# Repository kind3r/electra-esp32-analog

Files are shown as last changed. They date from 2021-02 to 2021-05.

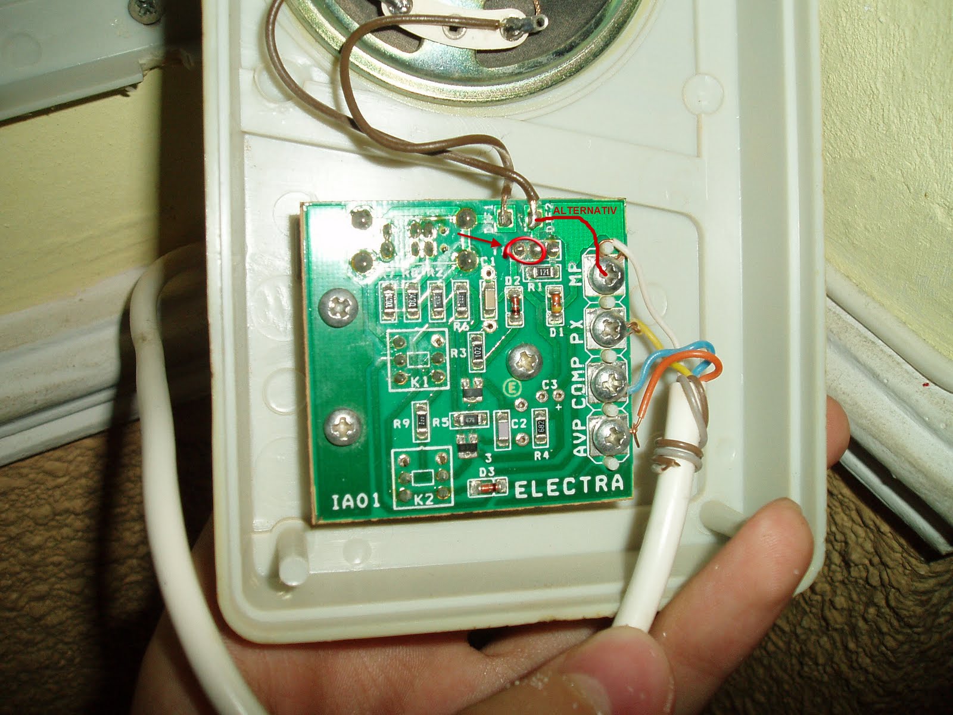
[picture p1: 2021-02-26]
docs/IA02-undressed.JPG

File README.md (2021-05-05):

# electra-esp32-analog

Turning an analogic Electra IA003/IA01/IA02 into a smart Home Assistant [lock device](https://www.home-assistant.io/integrations/lock/) using an ESP32-WROOM-32D module and a few extra components.

> **WARNING**: This project is a work in progress. Use at own risk.

Feeling generous and want to support my work, here is [my PayPal link](https://paypal.me/kind3r).

## Intro

After some research and experimentation it was **not possible to power the ESP32 module from the intercom power line** as the power is not always available and the ESP32 WiFi and boot power drain spikes confuse the Electra Call Distributor. So the next logical step was to use a battery to power the device. 

Regular **rechargeable Li-Ion** batteries are commonly available ini different shapes and sizes. The problem is that they charge up to about 4.2V so they require some voltage drop to be able to power the ESP32. Since the device only wakes up when the intercom is riniging and voltage drop circuit consumes power all the time, this makes using such batteries inefficient (and I am a big fan of optimisation). There are of course more efficient LDO's like TI's [TPS62841DGRR](https://ro.mouser.com/ProductDetail/595-TPS62841DGRR) but those are hard to find currently.

At first I opted for a rechargeable **LiFePO4 18650** battery to optimise power usage since it's nominal voltage is 3.2V and it's max charge is 3.6V, thus it does not require power regulation which saves quite some energy. Combined with the fact that the device is mostly in deep sleep mode, this should give a **very long battery life** (few years - still need to make exact measuremets). Unfortunatelly LiFePO4 batteries and chargers (I had to build my own) do not seem to be that common making which raises the cost of (also time to build) the device. 

Now I am testing 2 **alkaline AAA** batteries and it seems to work fine and they also fit in the intercom case, event better than the 18650 but due to their discharge curve only about 30% of their capacity will be used (which still would provide up to a year of usage). But then you are throwinig away 2/3 of the battery (unless you move it to a remote control or some other AAA powered device). Not ideal. 

Another option would be using **lithium AAA** batteries which are available locally (not as much as alkaline AAA, but still). While a bit more expensive than the regular alkaline AAA, their discharge curve is optimal for powering the ESP32, providinig a similar life to the rechargeable LiFePO4. 

## Features

- Easy configuration via Soft AP and browser UI
  - Automatically enter config mode in case of errors
  - Manually enter config mode using dedicated button
- [Home Assistant](https://www.home-assistant.io/) integration via MQTT
  - Ringing status
  - Unlock
  - Battery life reporting
  - Configure automations
- Ultra low power usage
  - Deep sleep when not ringing
  - Deep sleep after 5 min if in configuration mode 
- LED status
  - Slow blink: Configuration mode
  - Fast blink: Ringing
- Optically isolated from intercom's lines, no risk of damaging the ESP32 module
- Fits inside the intercom's enclosure

## How To

### Build your device

Schematic, PCB and BOM are available [here](https://oshwlab.com/Gibonii/electra-ia003-ia01-esp). 

> **WARNING**: Schematic and PCB not yet final, I might still make adjustments. Rev.4 is currently under testing and working fine. 

> TODO: how to order PCBs and assembly

> TODO: explain extra components required:
> - JST-SH-6 + VoltLink or USB2TTL
> - JST-SH-3 for intercom interface
> - JST-XH-2 and LiFePO4 battery + holder

### Upload software

> TODO: 
> - Connector for uploading
> - How to build and make configuration adjustments (battery reporting interval, configuration mode sleep time)
> - PlatformIO + upload SPIFFS (for web config) & config file (optional)

### Configuration

> TODO: 
> - HA preparations
> - First time configuration
> - Testing

## Resources of inspiration

- [https://micro-flight.blogspot.com/2010/09/hack-interfon-electra.html](https://micro-flight.blogspot.com/2010/09/hack-interfon-electra.html)
- [https://forum.arduino.cc/index.php?topic=659051.0](https://forum.arduino.cc/index.php?topic=659051.0)

## TODO

Short term:
- Finish documentation
- Test power usage

Medium/long term:
- Make a changelog
- Provide other integrations besides Home Assistant

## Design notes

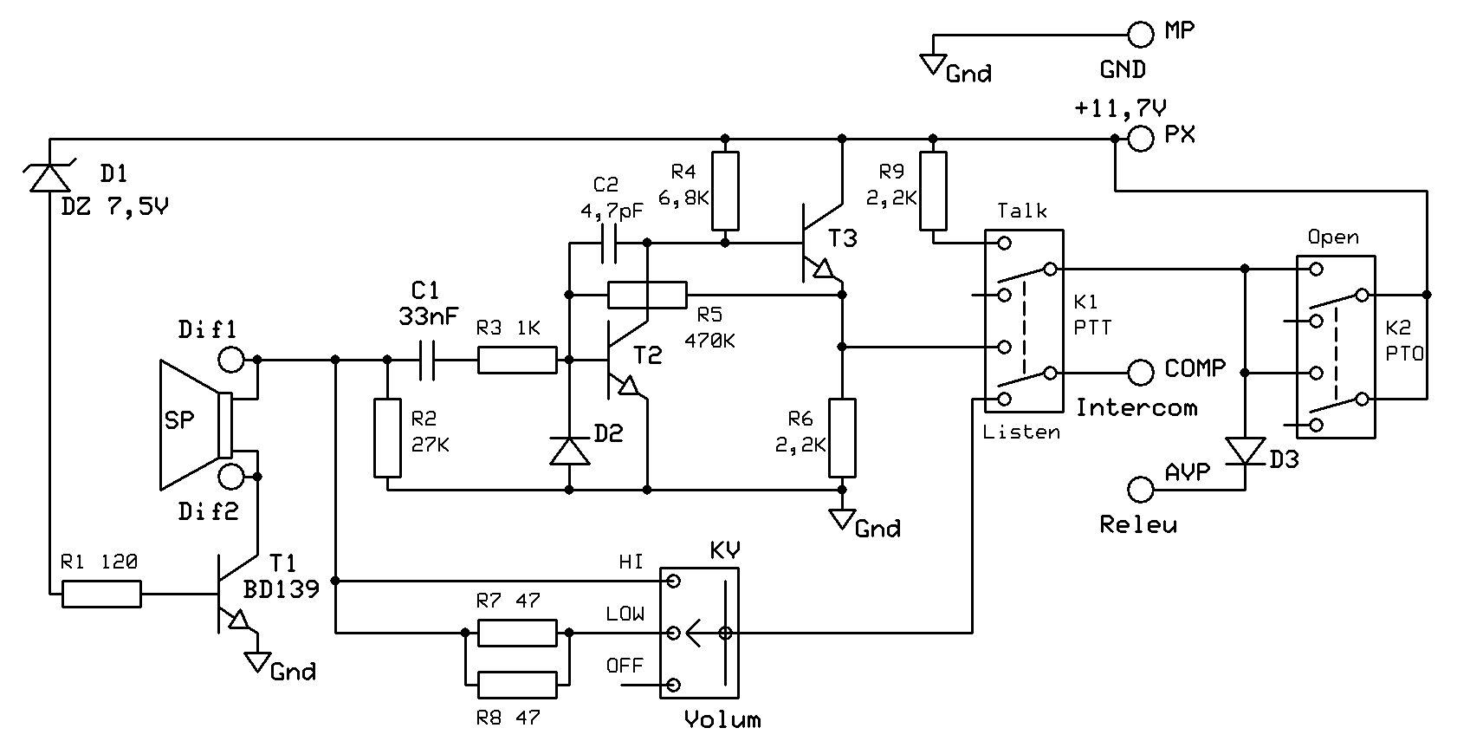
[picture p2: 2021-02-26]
docs/IA02-circuit.jpg

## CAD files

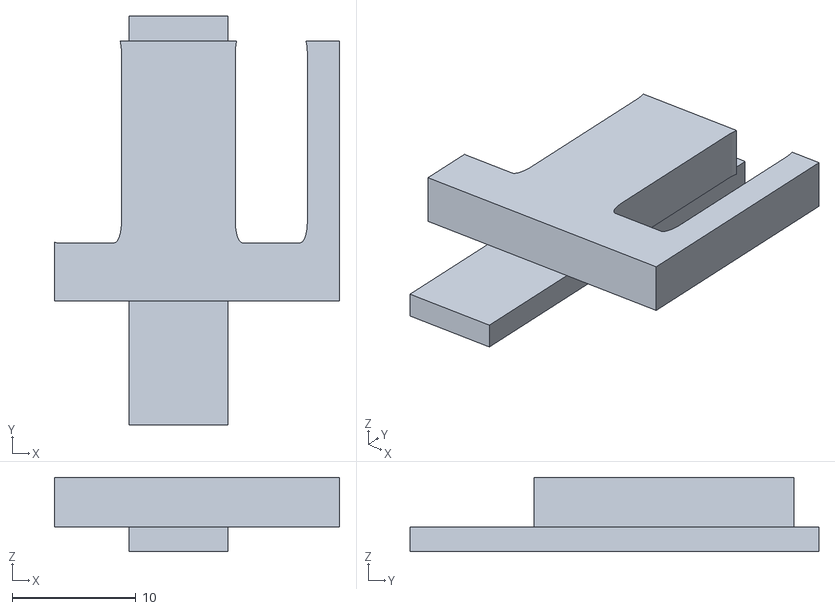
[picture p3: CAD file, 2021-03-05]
docs/other/Electra IA001 Buttons cover.stl
23.0 x 33.0 x 6.00

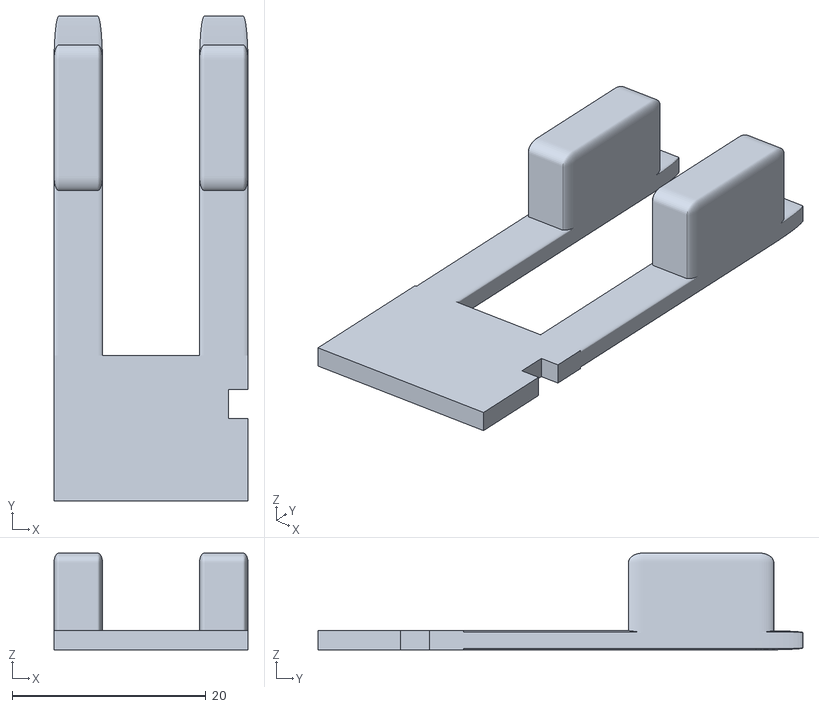
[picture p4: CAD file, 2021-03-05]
docs/other/Electra IA001 Buttons.stl
20.0 x 50.0 x 10.0

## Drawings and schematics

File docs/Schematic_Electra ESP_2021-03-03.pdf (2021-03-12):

## Intercom control

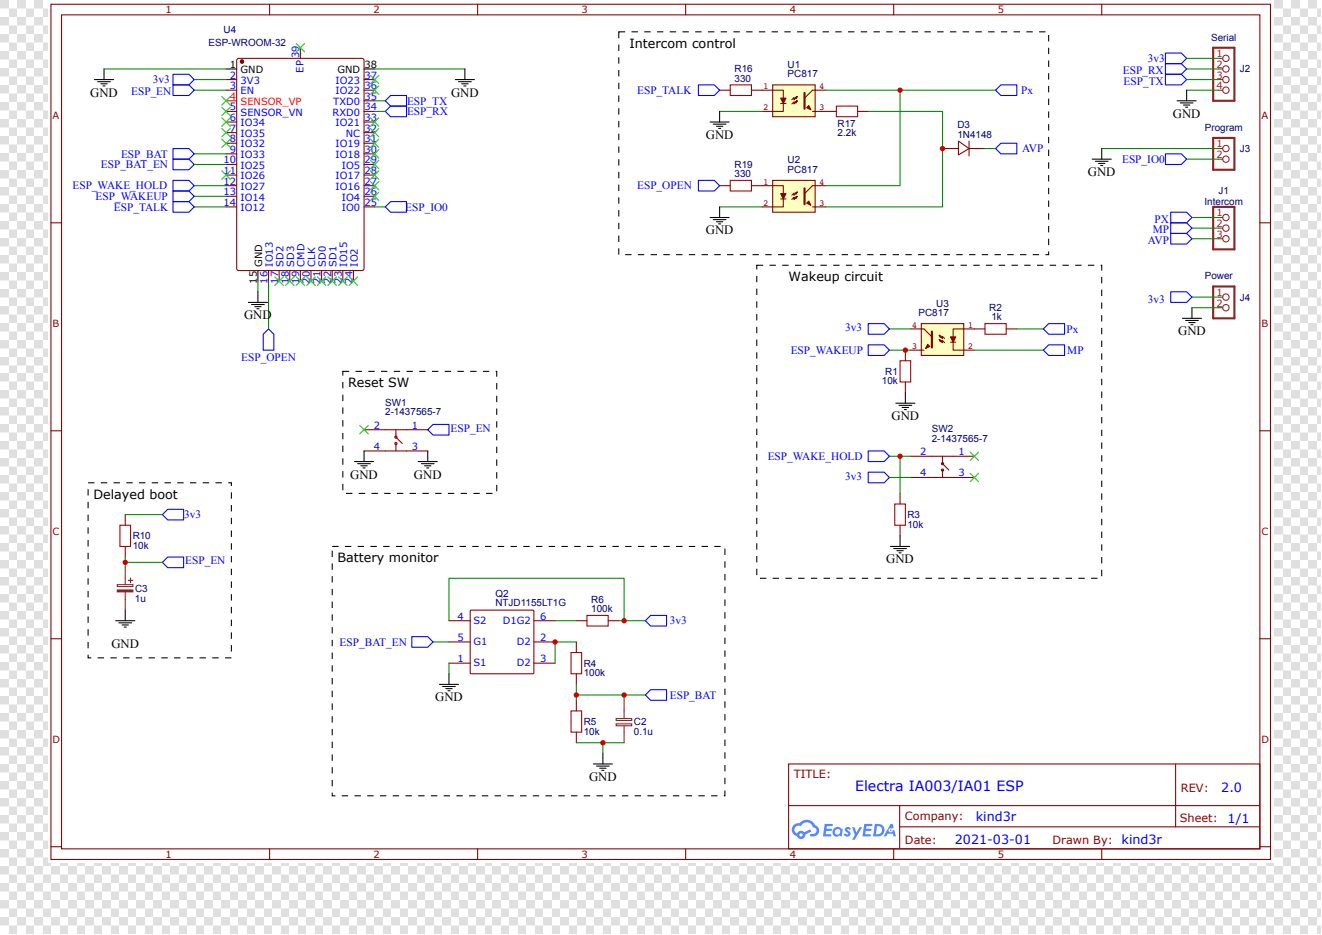
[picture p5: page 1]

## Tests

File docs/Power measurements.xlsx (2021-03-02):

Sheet: 240Mhz, 2654ms
Voltage-Current
Time | Voltage(V) | Current(A) | D+(V) | D-(V) | Date | Absolute (mA)
0.3016898148 | 4.98 | 0.017 | 3.07 | 0.18 | 44254 | 0
0.3017013889 | 4.98 | 0.017 | 3.06 | 0.19 | 44254 | 0
0.301712963 | 4.98 | 0.017 | 3.07 | 0.19 | 44254 | 0
0.301724537 | 4.98 | 0.019 | 3.08 | 0.19 | 44254 | 2
0.3017361111 | 4.96 | 0.06 | 3.05 | 0.19 | 44254 | 43
0.3017476852 | 4.95 | 0.084 | 3.07 | 0.19 | 44254 | 67
0.3017592593 | 4.95 | 0.084 | 3.08 | 0.19 | 44254 | 67
0.3017708333 | 4.96 | 0.062 | 3.06 | 0.19 | 44254 | 45
0.3017824074 | 4.96 | 0.058 | 3.07 | 0.18 | 44254 | 41
0.3017939815 | 4.95 | 0.099 | 3.07 | 0.17 | 44254 | 82
0.3018055556 | 4.96 | 0.075 | 3.07 | 0.2 | 44254 | 58
0.3018171296 | 4.96 | 0.066 | 3.06 | 0.2 | 44254 | 49
0.3018287037 | 4.96 | 0.074 | 3.07 | 0.19 | 44254 | 57
0.3018402778 | 4.96 | 0.065 | 3.07 | 0.2 | 44254 | 48
0.3018518519 | 4.96 | 0.067 | 3.07 | 0.18 | 44254 | 50
0.3018634259 | 4.97 | 0.017 | 3.06 | 0.18 | 44254 | 0
0.301875 | 4.98 | 0.018 | 3.07 | 0.18 | 44254 | 1
0.3018865741 | 4.98 | 0.017 | 3.06 | 0.18 | 44254 | 0
0.3018981481 | 4.97 | 0.017 | 3.07 | 0.2 | 44254 | 0
0.3019097222 | 4.98 | 0.017 | 3.06 | 0.19 | 44254 | 0
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

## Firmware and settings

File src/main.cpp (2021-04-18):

#include <esp_err.h>
#include <nvs_flash.h>
#include <esp_netif.h>
#include <esp_event.h>
#include "settings.h"
#include "ha.h"
#include "wifi.h"
#include "wifiap.h"
#include "util.h"
#include "intercom.h"
#include "sleep.h"
#include "battery.h"
#include "led.h"
#include "ota.h"
#include "spiffs.h"
#include "log.h"

extern "C"
{
  void app_main(void);
}

void app_main()
{
  ESP_ERROR_CHECK(nvs_flash_init());
  ESP_ERROR_CHECK(esp_netif_init());
  ESP_ERROR_CHECK(esp_event_loop_create_default());

  Spiffs::init();
  
  LOG::init();
  
  Led::init();

  Battery::init();

  Intercom::init();

  Sleep::init();

  if (Settings::init() != ESP_OK)
  {
    ESP_LOGE("main", "Error during Settings init");
    // enter config mode
    WiFiAP::init();
    Sleep::start(300); // sleep after 5 minutes
  }
  else
  {
    Ota::init();
    if (HA::init() != ESP_OK)
    {
      ESP_LOGE("main", "Error during HA init");
      Sleep::start();
    }
    else if (WiFi::init() != ESP_OK)
    {
      ESP_LOGE("main", "Error during WiFi init");
      // Sleep::start();
      esp_restart();
    }
  }
}

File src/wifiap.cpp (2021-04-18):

#include "wifiap.h"
#include "dnsserver.h"

static const char *TAG = "WiFiAP";

httpd_handle_t WiFiAP::server = nullptr;
httpd_uri_t WiFiAP::home = {
    .uri = "/",
    .method = HTTP_GET,
    .handler = handleHome,
    .user_ctx = NULL};
httpd_uri_t WiFiAP::configGet = {
    .uri = "/config",
    .method = HTTP_GET,
    .handler = handleConfigGet,
    .user_ctx = NULL};
httpd_uri_t WiFiAP::configSet = {
    .uri = "/config",
    .method = HTTP_POST,
    .handler = handleConfigSet,
    .user_ctx = NULL};
httpd_uri_t WiFiAP::logsGet = {
    .uri = "/logs",
    .method = HTTP_GET,
    .handler = handleLogsGet,
    .user_ctx = NULL};
httpd_uri_t WiFiAP::logGet = {
    .uri = "/log/*",
    .method = HTTP_GET,
    .handler = handleLogGet,
    .user_ctx = NULL};
uint8_t *WiFiAP::buffer = new uint8_t[ELECTRA_ESP_CONFIG_BUFFER_SIZE];
logFiles_t WiFiAP::logs;

void WiFiAP::init()
{
  mdns_start();
  wifi_init_softap();
  Led::blinkSlow();
}

void WiFiAP::startWebServer()
{
  if (server == nullptr)
  {
    httpd_config_t config = HTTPD_DEFAULT_CONFIG();
    config.max_open_sockets = 3;
    config.uri_match_fn = httpd_uri_match_wildcard;
    // config.stack_size = 8192;

    httpd_start(&server, &config);
    httpd_register_uri_handler(server, &home);
    httpd_register_uri_handler(server, &configGet);
    httpd_register_uri_handler(server, &configSet);
    httpd_register_uri_handler(server, &logsGet);
    httpd_register_uri_handler(server, &logGet);
  }
}

void WiFiAP::event_handler(void *arg, esp_event_base_t event_base, int32_t event_id, void *event_data)
{
  if (event_base == WIFI_EVENT && event_id == WIFI_EVENT_STA_START)
  {
    esp_wifi_connect();
  }
  else if (event_id == WIFI_EVENT_AP_STACONNECTED)
  {
    wifi_event_ap_staconnected_t *event = (wifi_event_ap_staconnected_t *)event_data;
    ESP_LOGI(TAG, "station " MACSTR " join, AID=%d", MAC2STR(event->mac), event->aid);
    startWebServer();
  }
  else if (event_id == WIFI_EVENT_AP_STADISCONNECTED)
  {
    wifi_event_ap_stadisconnected_t *event = (wifi_event_ap_stadisconnected_t *)event_data;
    ESP_LOGI(TAG, "station " MACSTR " leave, AID=%d", MAC2STR(event->mac), event->aid);
  }
}

void WiFiAP::wifi_init_softap()
{
  esp_netif_create_default_wifi_ap();

  wifi_init_config_t cfg = WIFI_INIT_CONFIG_DEFAULT();
  ESP_ERROR_CHECK(esp_wifi_init(&cfg));

  ESP_ERROR_CHECK(esp_event_handler_instance_register(WIFI_EVENT,
                                                      ESP_EVENT_ANY_ID,
                                                      &event_handler,
                                                      NULL,
                                                      NULL));

  wifi_config_t wifi_config = {};
  strcpy((char *)wifi_config.ap.ssid, ELECTRA_ESP_WIFI_CONFIG_SSID);
  wifi_config.ap.ssid_len = strlen(ELECTRA_ESP_WIFI_CONFIG_SSID);
  strcpy((char *)wifi_config.ap.password, ELECTRA_ESP_WIFI_CONFIG_PASS);
  wifi_config.ap.channel = ELECTRA_ESP_WIFI_CONFIG_CHANNEL;
  wifi_config.ap.max_connection = ELECTRA_ESP_WIFI_CONFIG_MAX_CONNECTIONS;
  wifi_config.ap.authmode = WIFI_AUTH_WPA2_PSK;

  ESP_ERROR_CHECK(esp_wifi_set_mode(WIFI_MODE_AP));
  ESP_ERROR_CHECK(esp_wifi_set_config(WIFI_IF_AP, &wifi_config));
  ESP_ERROR_CHECK(esp_wifi_start());

  ESP_LOGI(TAG, "wifi_init_softap finished. SSID:%s password:%s channel:%d",
           ELECTRA_ESP_WIFI_CONFIG_SSID, ELECTRA_ESP_WIFI_CONFIG_PASS, ELECTRA_ESP_WIFI_CONFIG_CHANNEL);

  // Setup DNS server to respond to name.local
  char hostname[strlen(ELECTRA_ESP_WIFI_HOSTNAME) + 7];
  memcpy(hostname, ELECTRA_ESP_WIFI_HOSTNAME, strlen(ELECTRA_ESP_WIFI_HOSTNAME));
  memcpy(hostname + strlen(ELECTRA_ESP_WIFI_HOSTNAME), ".local", 6);
  hostname[strlen(ELECTRA_ESP_WIFI_HOSTNAME) + 7] = '\0';
  init_dns_server(hostname);
}

esp_err_t WiFiAP::handleHome(httpd_req_t *req)
{
  FILE *fd = nullptr;
  fd = fopen("/spiffs/index.html.gz", "r");
  if (!fd)
  {
    ESP_LOGE(TAG, "Failed to read index.html.gz from SPIFFS");
    /* Respond with 500 Internal Server Error */
    httpd_resp_send_err(req, HTTPD_500_INTERNAL_SERVER_ERROR, "Failed to read existing file");
    return ESP_FAIL;
  }

  // set content type and encoding
  httpd_resp_set_type(req, "text/html");
  httpd_resp_set_hdr(req, "Content-Encoding", "gzip");

  /* Retrieve the pointer to scratch buffer for temporary storage */
  size_t chunksize;
  do
  {
    /* Read file in chunks into the scratch buffer */
    chunksize = fread(buffer, 1, ELECTRA_ESP_CONFIG_BUFFER_SIZE, fd);

    if (chunksize > 0)
    {
      /* Send the buffer contents as HTTP response chunk */
      if (httpd_resp_send_chunk(req, (char *)buffer, chunksize) != ESP_OK)
      {
        fclose(fd);
        ESP_LOGE(TAG, "File sending failed!");
        /* Abort sending file */
        httpd_resp_sendstr_chunk(req, NULL);
        /* Respond with 500 Internal Server Error */
        httpd_resp_send_err(req, HTTPD_500_INTERNAL_SERVER_ERROR, "Failed to send file");
        return ESP_FAIL;
      }
    }

    /* Keep looping till the whole file is sent */
  } while (chunksize != 0);

  /* Send empty chunk to signal HTTP response completion */
  httpd_resp_sendstr_chunk(req, NULL);

  fclose(fd);

  return ESP_OK;
}

esp_err_t WiFiAP::handleConfigGet(httpd_req_t *req)
{
  httpd_resp_set_type(req, HTTPD_TYPE_JSON);

  size_t len = Settings::getConfigFile(buffer);
  buffer[len] = '\0';

  httpd_resp_sendstr(req, (char *)buffer);

  return ESP_OK;
}

esp_err_t WiFiAP::handleConfigSet(httpd_req_t *req)
{
  int total_len = req->content_len;
  int cur_len = 0;
  int received = 0;
  if (total_len >= ELECTRA_ESP_CONFIG_BUFFER_SIZE)
  {
    /* Respond with 500 Internal Server Error */
    httpd_resp_send_err(req, HTTPD_500_INTERNAL_SERVER_ERROR, "content too long");
    return ESP_FAIL;
  }
  while (cur_len < total_len)
  {
    received = httpd_req_recv(req, (char *)buffer + cur_len, total_len);
    if (received <= 0)
    {
      /* Respond with 500 Internal Server Error */
      httpd_resp_send_err(req, HTTPD_500_INTERNAL_SERVER_ERROR, "Failed to post control value");
      return ESP_FAIL;
    }
    cur_len += received;
  }
  buffer[total_len] = '\0';

  httpd_resp_set_type(req, "text/html");
  if (Settings::putConfigFile(buffer, total_len + 1) == ESP_OK)
  {
    httpd_resp_sendstr(req, "OK");
    // reboot
    xTaskCreate(rebootTask, "reboot_task", 2048, NULL, 10, NULL);
  }
  else
  {
    httpd_resp_sendstr(req, "FAIL");
  }

  return ESP_OK;
}
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

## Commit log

2021-02-20 Initial commit, settings and wifi
    [min_spiffs.csv]
2021-02-21 Settings refactor, add mqtt, add schematics
2021-02-26 Add original schema, update open to recover in case ESP is still powered
2021-03-02 Add future battery measurement, add sleep and wake up, revert brownout lvl, HA config optimisation
    [Power measurements.xlsx]
2021-03-02 Start sleep monitor on init errors or mqtt activity and reduce wait time
    [main.cpp]
2021-03-05 Battery voltage reading with rough percent estimation
2021-03-05 Button covers stls
    [Electra IA001 Buttons cover.stl, Electra IA001 Buttons.stl]
2021-03-12 Add small delay to make battery reading more precise
2021-03-12 Add schematics and readme
    [Electra IA001 Buttons cover.stl, Electra IA001 Buttons.stl]
2021-03-16 Fix LWT battery reporting
2021-03-28 Remove redundant status updates. Add 3h wakeup for battery reporting.
2021-03-28 Add battery voltage sensor. Remove wake hold.
2021-03-29 WPA only AP and change SPIFFS size
    [min_spiffs.csv]
2021-03-29 Reboot after saving config. Auto sleep after 5 min in config mode.
    [main.cpp, wifiap.cpp]
2021-03-29 Force setup mode on wifi or mqtt errors
    [settings.cpp]
2021-03-30 Fix configuration save and auto enter config mode
    [main.cpp, settings.cpp]
2021-03-31 Untested LED blink patterns
2021-03-31 Finish LED implementation
2021-03-31 Add config button
2021-04-09 Update battery calibration for 2xAAA
2021-04-18 WIP: Add SPIFFS logs + API. Fix some http bugs.
    [min_spiffs.csv, partitions.csv]
